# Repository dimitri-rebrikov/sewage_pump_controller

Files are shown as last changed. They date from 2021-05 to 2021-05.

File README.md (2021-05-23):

# sewage_pump_controller
Electronic controller for sewage pump. Elektronische Steuerung für Abwasserpumpe.

This project implements a simple sewage pump controller.

The project is created using the KiCAD tool.

The advantages of the schematic is the simplicity and that the only one probe is necessary.
The disadvantage is that you need to detect the time the pump needs to emptify the sewage container and then setup this time using the trim pot RV1.

The time formula is 1.1(R3+RV1)C3 and is currently from 5 to 10 sec.
If you need longer time feel free to incerase R3 or RV1 or C3.
If you need shorter time pay attention that the R3 shall not be decreased as otherwise the Q1 which is connected over D1 will stop working in key mode.
Instead just decrease the C3. 

For the power supply I used just a common USB mobile phone charger.

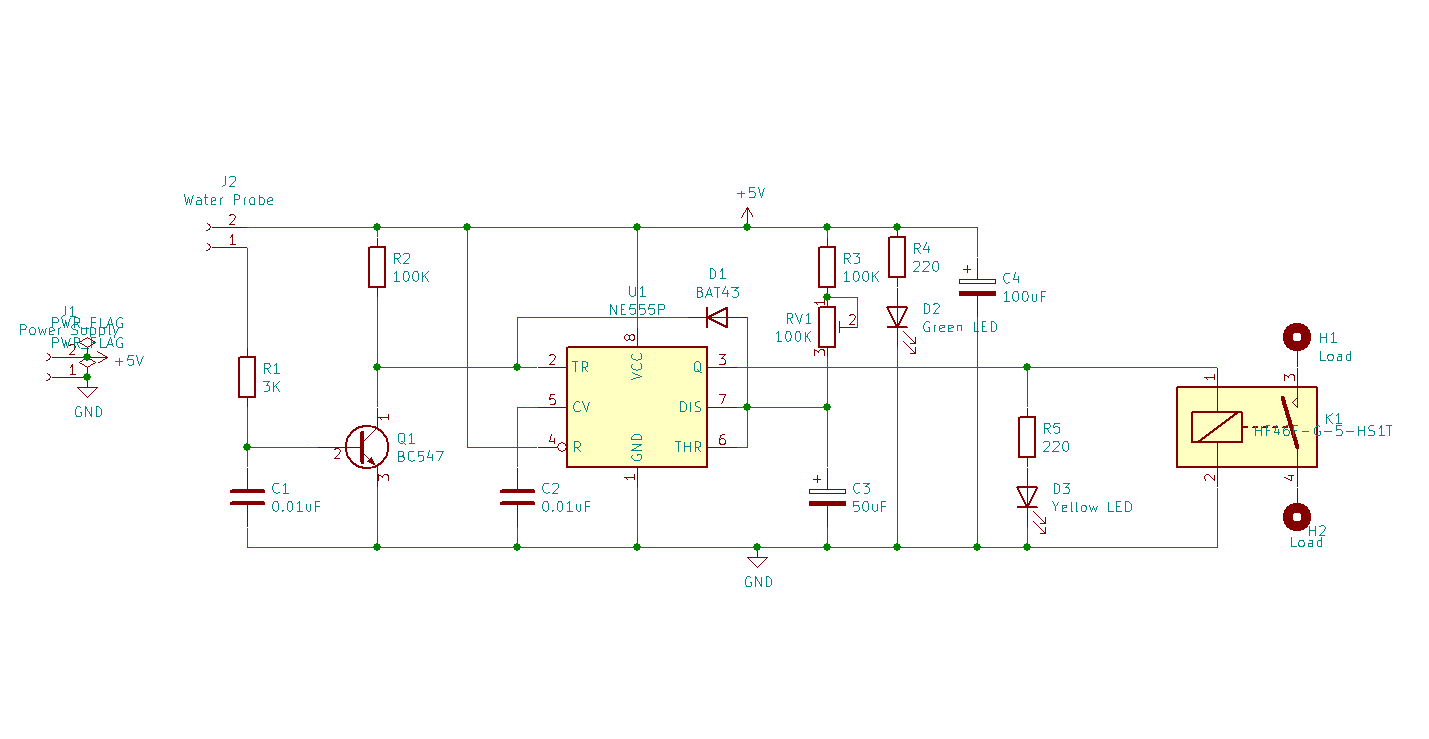
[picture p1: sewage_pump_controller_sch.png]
Circuit Diagram

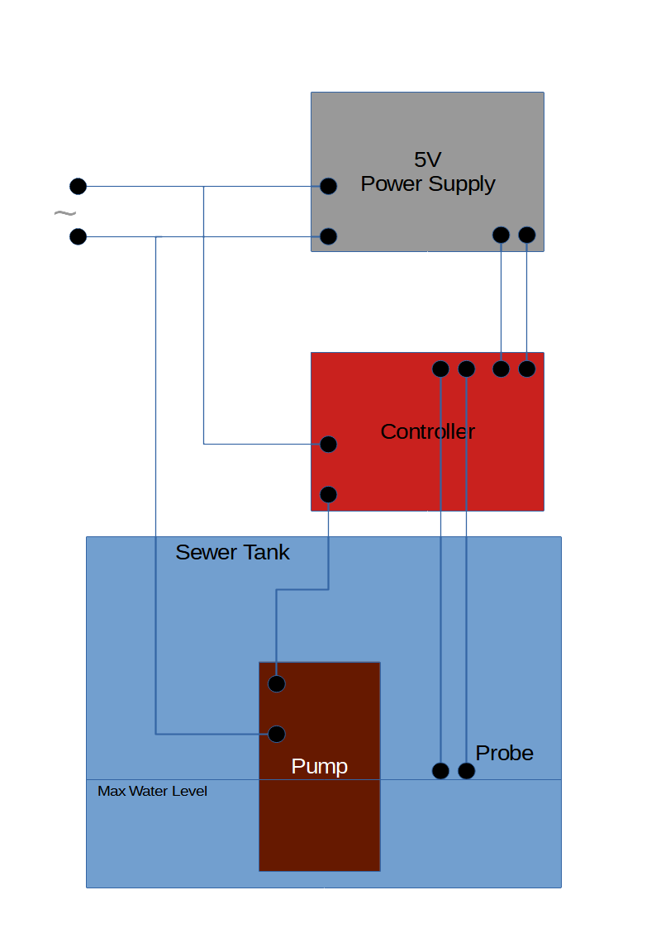
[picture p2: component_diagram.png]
Component Diagram

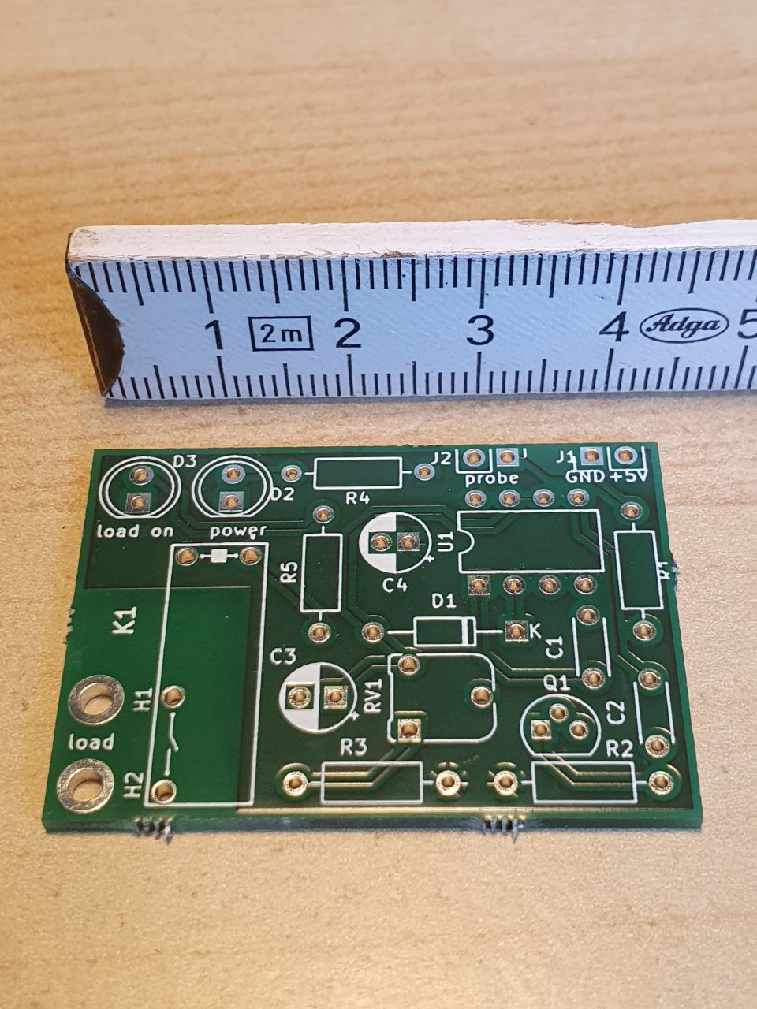
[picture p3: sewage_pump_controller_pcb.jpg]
PCB

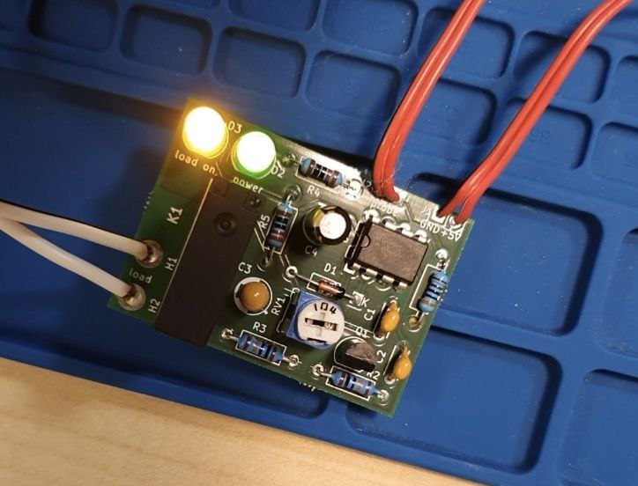
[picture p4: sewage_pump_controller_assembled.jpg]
Assembled


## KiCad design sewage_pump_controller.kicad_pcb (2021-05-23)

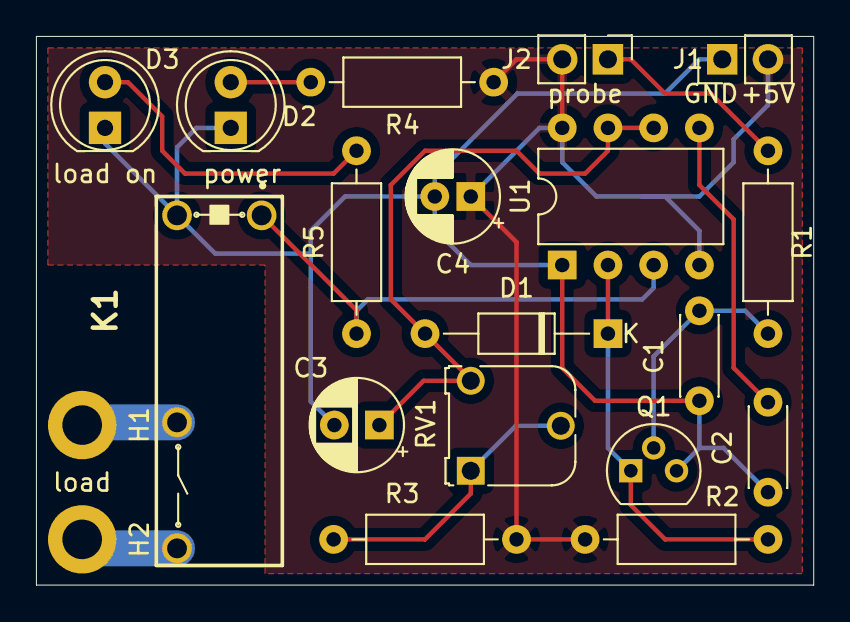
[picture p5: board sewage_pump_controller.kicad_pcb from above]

Board: 2 copper layers, 43.2 x 30.5 mm, 20 parts (0 on the bottom side), 13 nets.

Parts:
C1, C2: 0.01uF; C_Disc_D4.3mm_W1.9mm_P5.00mm
C3: 50uF; CP_Radial_D5.0mm_P2.50mm
C4: 100uF; CP_Radial_D5.0mm_P2.00mm
D1: BAT43; D_DO-35_SOD27_P10.16mm_Horizontal
D2: Green LED; LED_D5.0mm
D3: Yellow LED; LED_D5.0mm
H1, H2: MountingHole_Pad; MountingHole_2.2mm_M2_DIN965_Pad
J1, J2: Conn_01x02; PinHeader_1x02_P2.54mm_Vertical
K1: HF46F-G-5-HS1T; HF46F
Q1: BC547; TO-92
R1: 3K; R_Axial_DIN0207_L6.3mm_D2.5mm_P10.16mm_Horizontal
R2, R3: 100K; R_Axial_DIN0207_L6.3mm_D2.5mm_P10.16mm_Horizontal
R4, R5: 220; R_Axial_DIN0207_L6.3mm_D2.5mm_P10.16mm_Horizontal
RV1: 100K; Potentiometer_Runtron_RM-065_Vertical
U1: NE555P; DIP-8_W7.62mm

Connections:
+5V: C4.1, J1.2, J2.2, R2.1, R3.1, R4.1, U1.4, U1.8
GND: C1.2, C2.2, C3.2, C4.2, D2.1, D3.1, J1.1, K1.2, Q1.3, U1.1
unnamed: C1.1, Q1.2, R1.2
unnamed: C2.1, U1.5
unnamed: C3.1, D1.2, RV1.3, U1.6, U1.7
unnamed: D1.1, Q1.1, R2.2, U1.2
unnamed: D2.2, R4.2
unnamed: D3.2, R5.2
unnamed: H1.1, K1.3
unnamed: H2.1, K1.4
unnamed: J2.1, R1.1
unnamed: K1.1, R5.1, U1.3
unnamed: R3.2, RV1.1, RV1.2

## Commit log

2021-05-23 added pictures of the PCD and the assembled controller
2021-05-23 added comment about power supply
